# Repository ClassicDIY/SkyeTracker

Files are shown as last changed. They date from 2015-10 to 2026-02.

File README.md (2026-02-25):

# SkyeTracker

<a href="https://www.buymeacoffee.com/r4K2HIB" target="_blank">Buy Me A Coffee</a>




## Dual Axis solar tracker.

This project uses a pair of linear actuators to move a set of solar panels so that they face the sun throughout the day.
Knowing the latitude, longitude and the date/time, the software calculates the azimuth and elevation of the sun. The system is setup and calibrated using an Android app that communicates with the device using the Bluetooth interface. It has support for an anemometer, moving the solar panel array to horizontal position when the wind exceeds 30km/h.

Check the <a href='https://github.com/ClassicDIY/SkyeTracker/wiki'> wiki </a> for more information.

Here are some <a href='https://www.youtube.com/playlist?list=PLblHpNAh7b6LoXEqofkJhKn6jD81Y85qT'> videos </a>.

<p align="center">
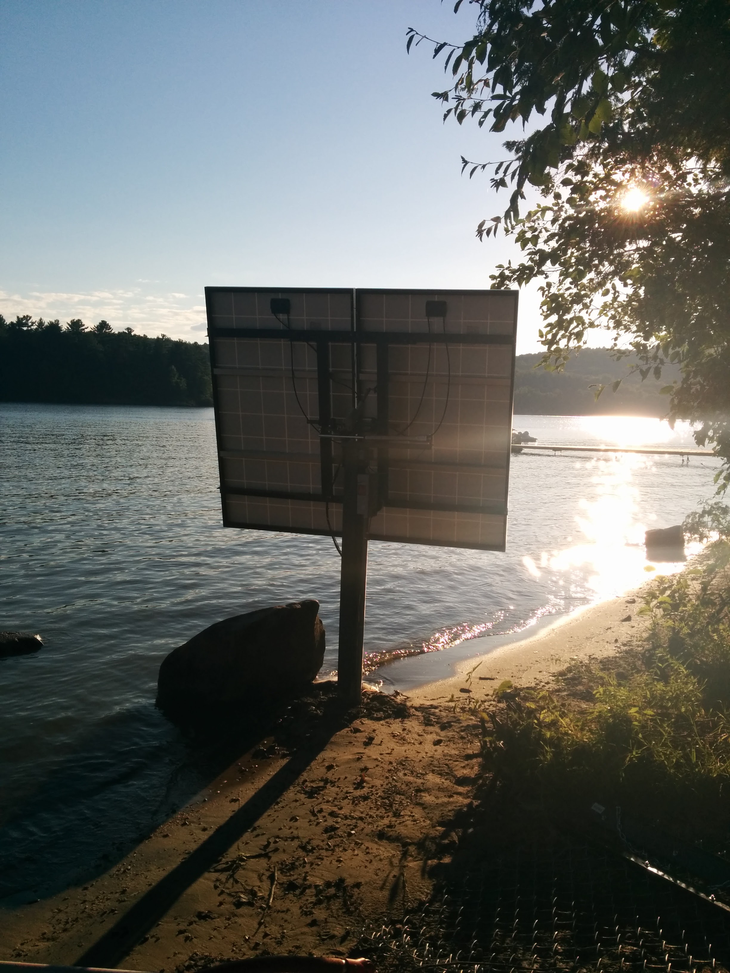
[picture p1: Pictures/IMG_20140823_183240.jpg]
  
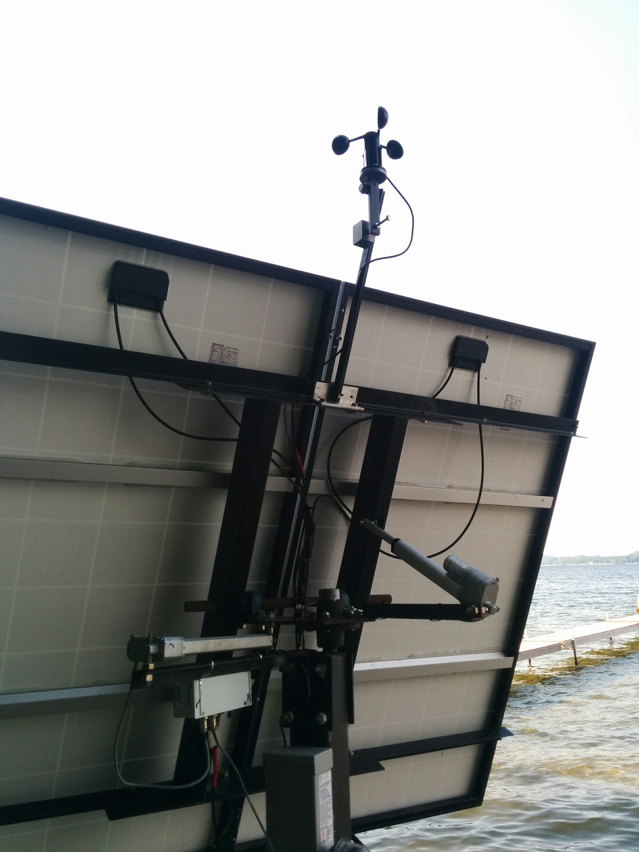
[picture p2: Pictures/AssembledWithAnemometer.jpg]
  
</p>

## SkyeTracker Wiring (Lilygo-T-Relay-S3)

New version 3 for the <a href='https://lilygo.cc/products/t-relay-s3'>Lilygo T-Relay-S3</a>

Note: Classic Bluetooth is no longer supported on the ESP32-S3 (now BLE only), support for the Android app has been removed.
The settings can be accessed via the Wifi Access Point, default AP: SkyeTracker default admin PW: 12345678

<p align="center">
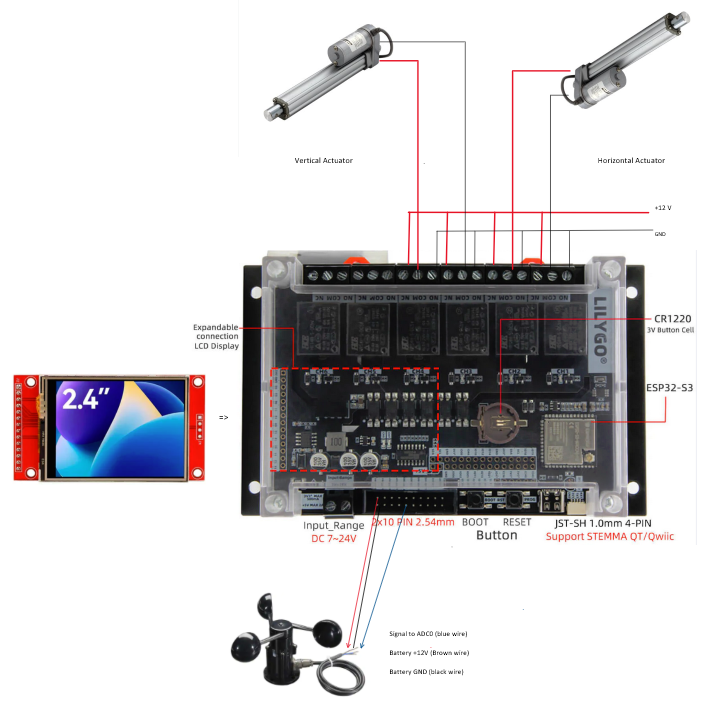
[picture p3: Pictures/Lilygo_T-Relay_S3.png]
  
</p>

<p align="center">
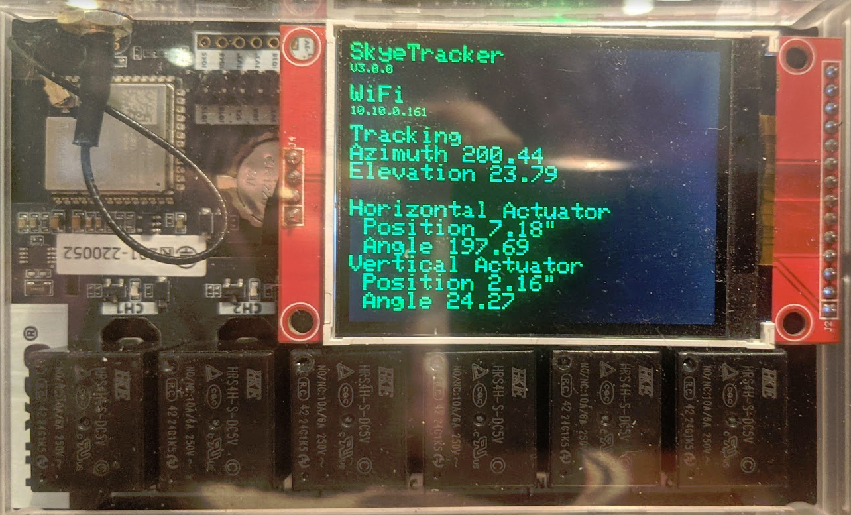
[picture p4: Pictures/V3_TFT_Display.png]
  
</p>

<p align="center">
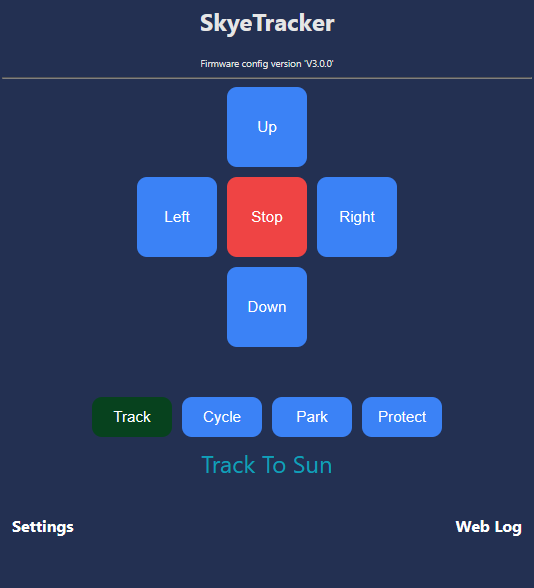
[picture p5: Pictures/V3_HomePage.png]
  
</p>

<p align="center">
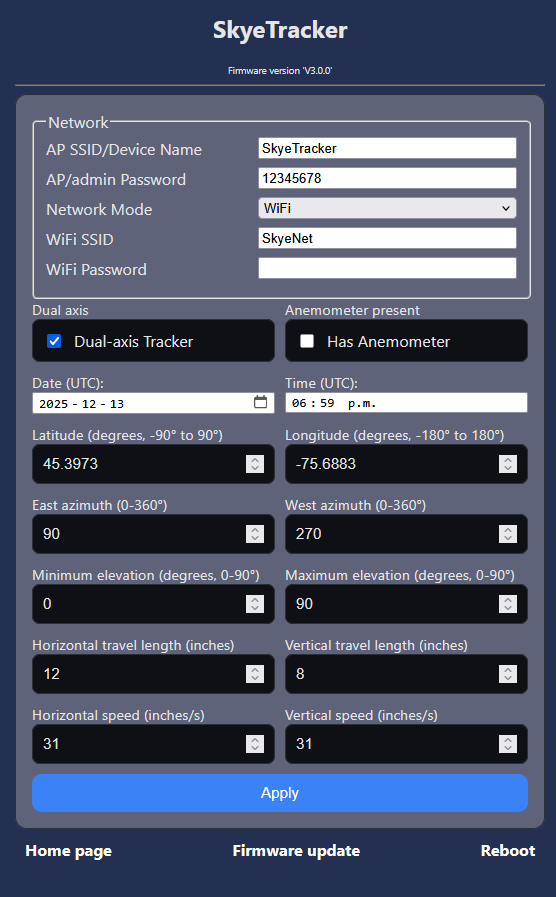
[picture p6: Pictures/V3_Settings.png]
  
</p>

<p align="center">
  
</p>

## SkyeTracker Wiring (ESP32 version 2)

Check the [wiki](https://github.com/ClassicDIY/SkyeTracker/wiki/4---ESP32-wiring-diagram) for updated information on the ESP32 implementation.

<p align="center">
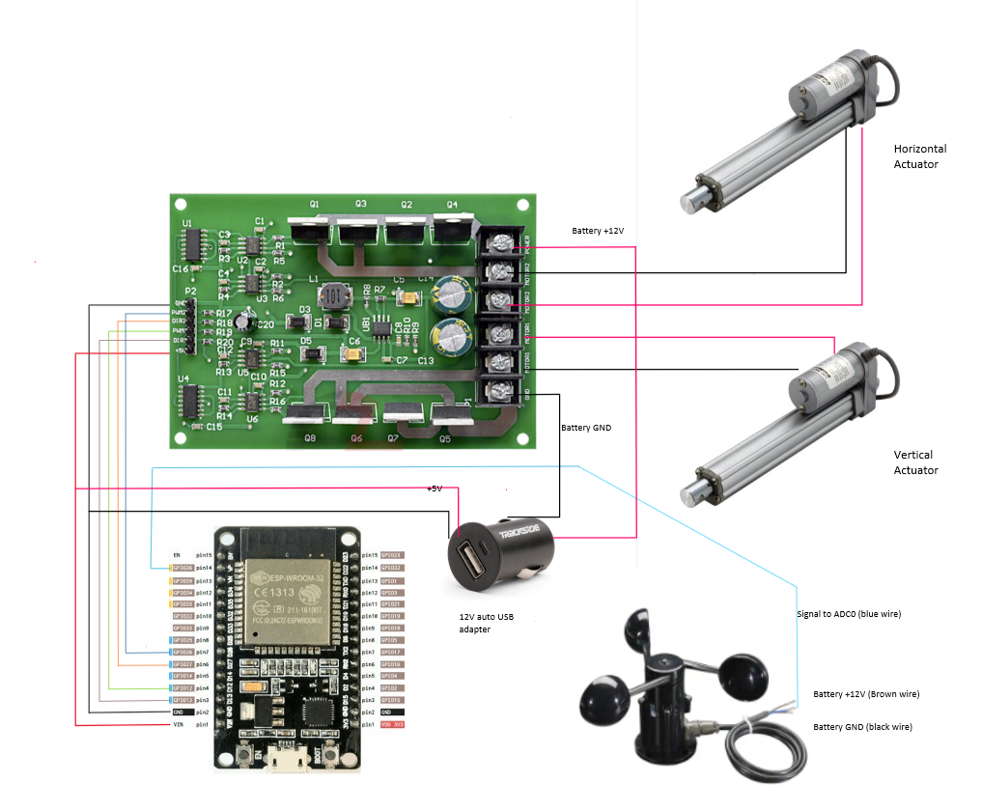
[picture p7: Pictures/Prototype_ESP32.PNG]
  
</p>

## Development tools:

<ul>
  <li>Visual Studio Code with PlatformIO IDE extension.</li>
  <li>Diptrace for schematic & PCB (NANO version).</li>
  <li>Sketchup for mechanical drawings.</li>
</ul>

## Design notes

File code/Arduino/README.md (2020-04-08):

# Arduino version of SkyeTracker 

<p align="center">
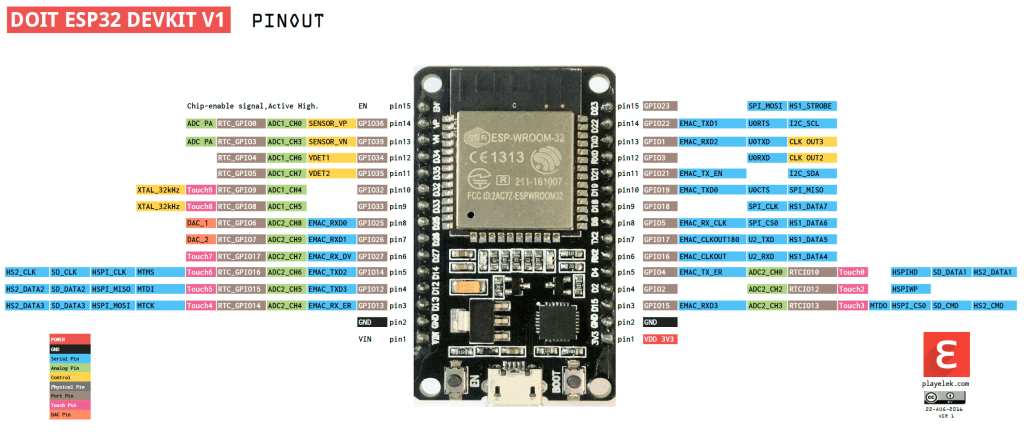
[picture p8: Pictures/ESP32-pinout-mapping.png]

</p>

Please refer to the [SkyeTracker wiki](https://github.com/ClassicDIY/SkyeTracker/wiki) for more information.

# Programming setup for the Arduino version of SkyeTracker

Once you downloaded and extracted the ZIP file for this project,
the code for the Arduino implementation is available in the `SkyeTracker-master\code\Arduino\SkyeTracker` directory.

This project uses Visual Studio CODE with the PlatformIO extension.
Here is a video tutorial for the VSCode & PlatformIO setup;
[PlatformIO for ESP32 Tutorial](https://www.youtube.com/watch?v=0poh_2rBq7E)

Once setup with the PlatformIO extension, use File->Open Folder to open the project selecting the `SkyeTracker-master\code\Arduino\SkyeTracker` folder.

The Arduino type can be set in the platform.ini.

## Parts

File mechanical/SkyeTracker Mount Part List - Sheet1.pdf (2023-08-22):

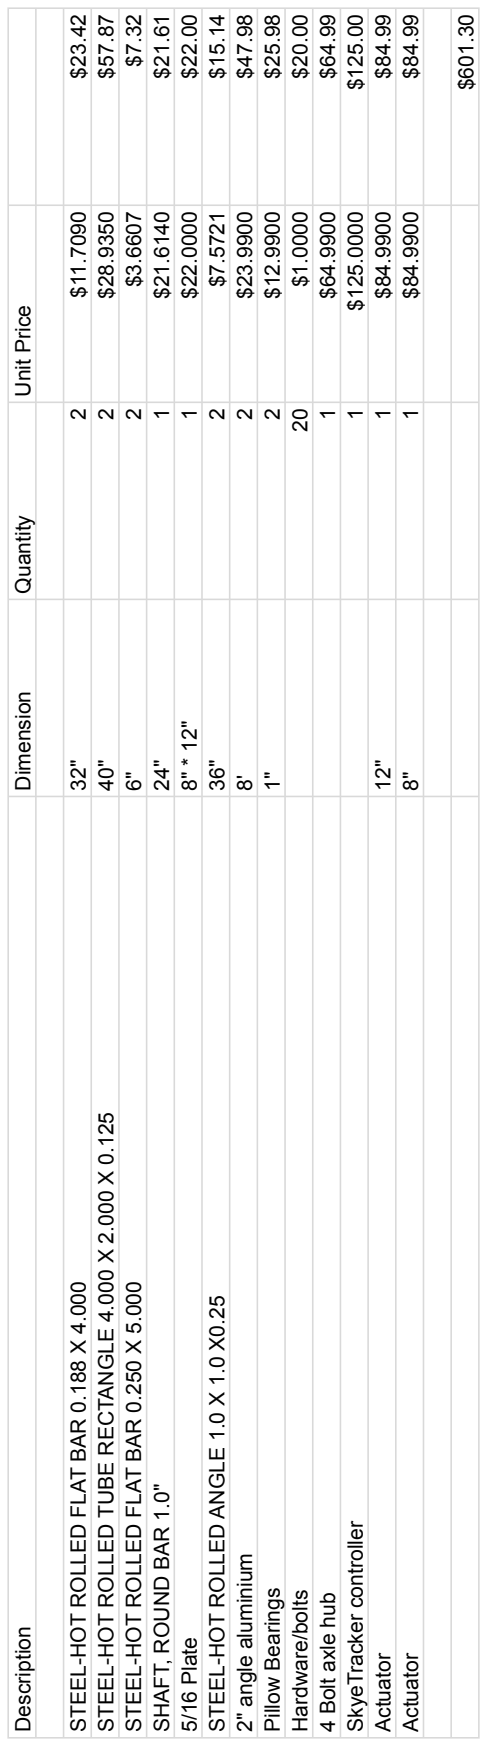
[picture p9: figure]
5/16 Plate 8" * 12" 1 $22.0000 $22.00; 2" angle aluminium 8' 2 $23.9900 $47.98; Pillow Bearings 1" 2 $12.9900 $25.98; Hardware/bolts 20 $1.0000 $20.00; 4 Bolt axle hub 1 $64.9900 $64.99; Actuator 12" 1 $84.9900 $84.99; Actuator 8" 1 $84.9900 $84.99

Description Dimension Quantity Unit Price

STEEL-HOT ROLLED FLAT BAR 0.188 X 4.000 32" 2 $11.7090 $23.42

STEEL-HOT ROLLED TUBE RECTANGLE 4.000 X 2.000 X 0.125 40" 2 $28.9350 $57.87

STEEL-HOT ROLLED FLAT BAR 0.250 X 5.000 6" 2 $3.6607 $7.32
SHAFT, ROUND BAR 1.0" 24" 1 $21.6140 $21.61

STEEL-HOT ROLLED ANGLE 1.0 X 1.0 X0.25 36" 2 $7.5721 $15.14 SkyeTracker controller 1 $125.0000 $125.00

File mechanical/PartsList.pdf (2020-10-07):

Description | Dimension | Length | Quantity | Price per foot | Unit Price | Price
Foot plate | 8" X .250 Flat bar | 8" | 1 | $17.80 | $12.00 | $12.00 metalsupermarkets.com
Gussets for foot plate | | | 8 | | $2.00 | $16.00
Post | 5" X 5" X .188" Square Tube | 60" | 1 | $24.00 | $120.00 | $120.00
Hub mounting plate | 5" X .188" Flat bar | 5 | 2 | $11.00 | $4.50 | $9.00
Bolts & Nuts for Hub plate | 3/8" X 6" | | 4 | | $2.00 | $8.00
Rotator Plate | 12" X 3/8" Flat bar | 12" | 1 | $30.00 | $30.00 | $30.00
Horizontal actuator arm | 1" X 1" angle | 23 3/8" | 1 | $7.00 | $14.00 | $14.00
Horizontal actuator arm mounting plate | 1" flat bar | 5" | 1 | $6.00 | $3.00 | $3.00
Horizontal actuator arm gusset | | | 1 | | $2.00 | $2.00
Vertical actuator arm | 1" X 1" angle | 15" | 1 | $7.00 | $8.75 | $8.75
H frame shaft | 1" | 23" | 1 | $10.00 | $19.20 | $19.20
H frame square tube | 4" X 2" X 0.125" square tube | 40" | 2 | $18.00 | $60.00 | $120.00
H frame end plates | 4" X 0.188" flat bar | 32" | 2 | $8.91 | $27.77 | $55.54
H frame sleeve | 3" X 1" I.D. | | 2 | | $11.80 | $23.60 Steel sleeve
Pillow Bearings | 1" | | 2 | | $12.18 | $24.36 Pillow-Block-Cast-Housing-Mounted
Bolts & Nuts for pillow bearings | 3/8" | 1.5" | 4 | | $1.50 | $6.00
4 Bolt axle hub | | | 1 | | $79.99 | $79.99 stub axle
SkyeTracker controller with box | | | 1 | | $100.00 | $100.00
Actuator | 12" | | 1 | | $84.99 | $84.99 12in linear actuator
Actuator | 8" | | 1 | | $84.99 | $84.99 8in linear actuator

$821.42

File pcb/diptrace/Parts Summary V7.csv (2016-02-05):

SkyeTracker V7
Column1 | Column2 | Column3
Part | Quantity | Stock | Unit Price | Sum | Link
CR1220 3.3v Lithium Coin Cells Button Battery | 1 | 21 | 0.194800 | $0.194800
CR1220 3.3v Lithium Coin Cells Button Battery holder | 1 | 1 | 0.650000 | $0.650000
50V 220UF SMD Aluminum Electrolytic Capacitors Size 10*10.2MM | 1 | 7 | 0.554500 | $0.554500
35v 220UF SMD Aluminum Electrolytic Capacitors Size 8x10mm | 2 | 54 | 0.708500 | $1.417000
0.1uf Ceramic capacitors SMD 0603 | 2 | 20 | 0.007327 | $0.014654
DO-214AC M7 SMA IN4007 SMD 1A | 8 | 63 | 0.049900 | $0.399200
SCHOTTKY SS54 5A 40V DO-214AC | 2 | 16 | 0.170000 | $0.340000
SMD 0805 Blue LED | 1 | 100 | 0.013720 | $0.013720
1206 SMD Resettable Fuse DC:32V 3A | 1 | 2 | 0.268000 | $0.268000
1206 SMD Resettable Fuse DC:32V 2A | 2 | 47 | 0.268000 | $0.536000
2Pin Plug-in Screw Terminal Block Connector 3.81mm Pitch Right Angle Orange | 1 | 20 | 0.543500 | $0.543500
2Pin Plug-in Screw Terminal Block Connector 3.81mm Pitch Right Angle Green | 2 | 20 | 0.720000 | $1.440000
INDUCTOR 12X12mm | 1 | 7 | 0.471000 | $0.471000
2.2k Resistor SMD 1206 | 2 | 100 | 0.005552 | $0.011104
634 Resistor SMD 1206 | 1 | 100 | 0.005552 | $0.005552
40pin Strip Tin PCB Female IC Breakable Single Row | 1 | 3 | 0.667000 | $0.667000
Arduino Nano V3.0 ATmega328 | 1 | 4 | 3.132000 | $3.132000
DS1307Z SMD SOP-8 | 1 | 9 | 0.130600 | $0.130600
HC_06 Bluetooth RF Transceiver Module | 1 | 4 | 4.134000 | $4.134000
L298N ZIP-15 ST DUAL FULL BRIDGE MOTOR DRIVER | 1 | 10 | 1.434000 | $1.434000
Screw for heat sink, 2.7 * 6mm | 1 | 10 | 0.059000 | $0.059000
Black Aluminum Heat Sink Heatsink for TO220 L298N | 1 | 7 | 0.443000 | $0.443000
LM2596S-12 TO-263 LM2596 12V Voltage Regulator | 1 | 4 | 0.693000 | $0.693000
SMD-2Pin 32.768K 32.768KHz Crystal 3.2mm×1.5mm | 1 | 40 | 1.384000 | $1.384000
PCB | 1 | 2 | 13.500000 | $13.500000
158x90x65mm Clear Waterproof Plastic Electronic Project Box Enclosure Cover CASE | 1 | 0 | 6.990000 | $6.990000 | http://www.ebay.ca/itm/158x90x65mm-Clear-Waterproof-Plastic-Electronic-Project-Box-Enclosure-Cover-CASE-/262063317709
Nylon Plastic stick on PCB Locking Snap-In Spacer Standoff 3mm Hole | 4 | 0 | 0.140500 | $0.562000 | http://www.ebay.ca/itm/221939473950?var=520828301848
Strain Relief Bushing for 5mm Round Cables | 3 | 0 | 0.080800 | $0.242400 | http://www.ebay.ca/itm/50pieces-Nylon-Wires-Protectors-Strain-Relief-Bushing-for-5mm-Round-Cables-/351136555494
 |  |  |  | $40.230030

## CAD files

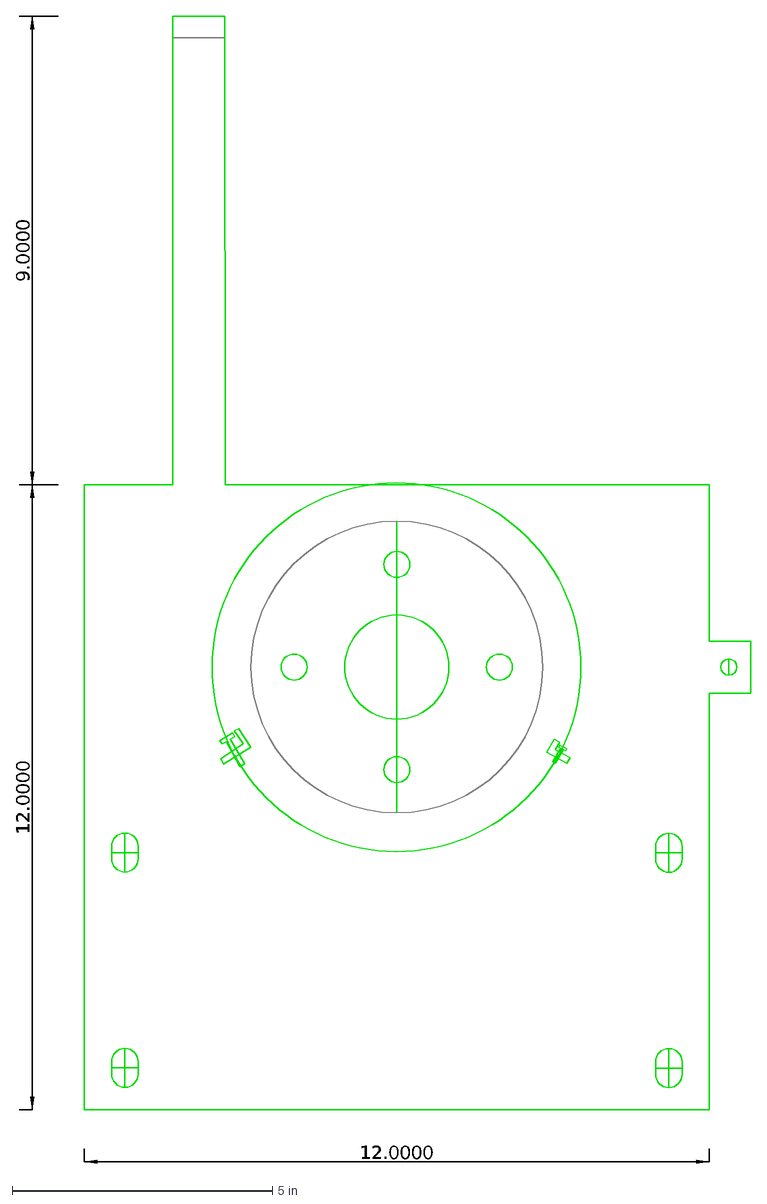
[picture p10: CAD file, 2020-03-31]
mechanical/LibreCAD/Bottom.dxf
9.0000
12.0000

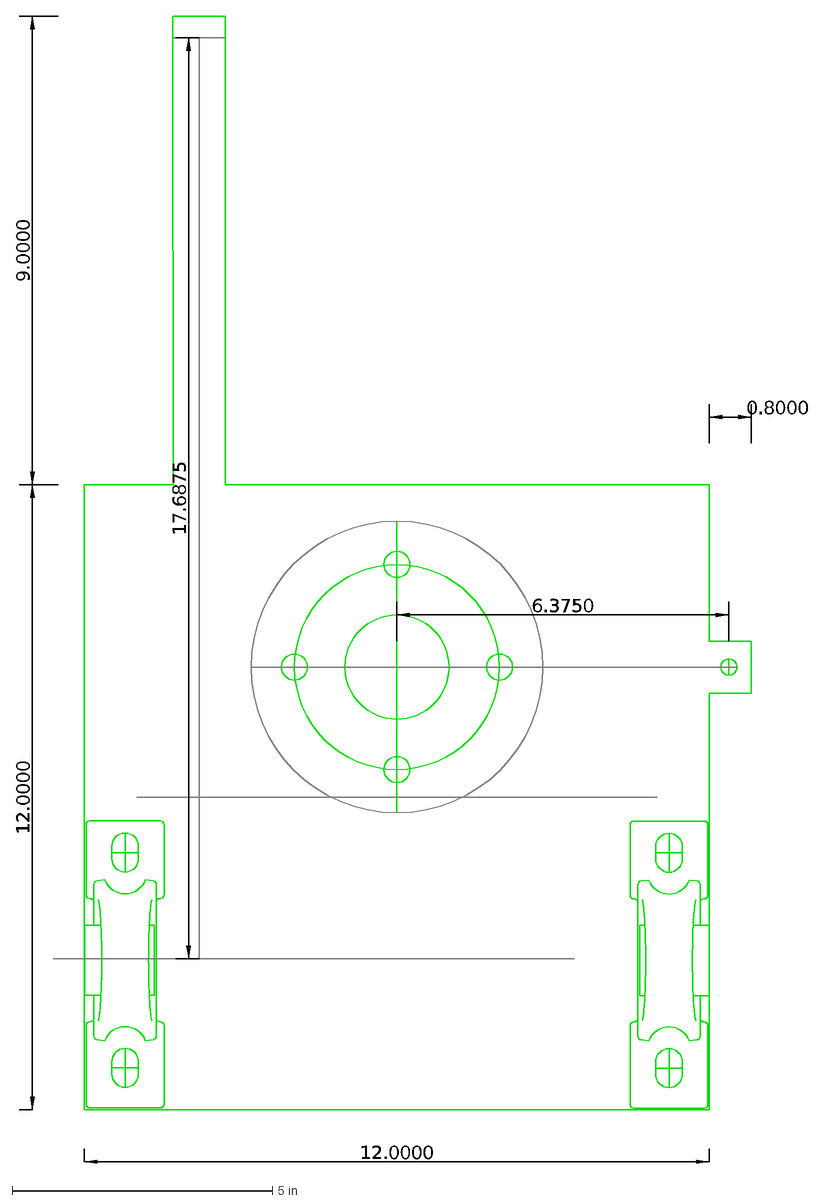
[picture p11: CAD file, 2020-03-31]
mechanical/LibreCAD/hub.dxf
6.3750
17.6875
9.0000
12.0000
0.8000

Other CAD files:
mechanical/TrackerFrame/Drawings/StubAxle.dwg
mechanical/Archive/Sketchup/Components/8L16.skp
mechanical/Archive/Sketchup/Components/FRAME2.skp
mechanical/Archive/Sketchup/Components/Linear Actuator 12 inch.skp
mechanical/Archive/Sketchup/Components/Linear Actuator 6 Inch.skp
mechanical/Archive/Sketchup/Components/Solar Panel 60 cell Kyocera.skp
mechanical/Archive/Sketchup/Components/Solar Panel 72 cell.skp
mechanical/Archive/Sketchup/Components/Vent.skp
mechanical/Archive/Sketchup/Models/Battery Box.skp
mechanical/Archive/Sketchup/Models/Dual Axis Tracker Assembly.skp
mechanical/Sketchup/Components/8L16.skp
mechanical/Sketchup/Components/FRAME2.skp
mechanical/Sketchup/Components/Linear Actuator 12 inch.skp
mechanical/Sketchup/Components/Linear Actuator 6 Inch.skp
mechanical/Sketchup/Components/Solar Panel 60 cell Kyocera.skp
mechanical/Sketchup/Components/Solar Panel 72 cell.skp
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

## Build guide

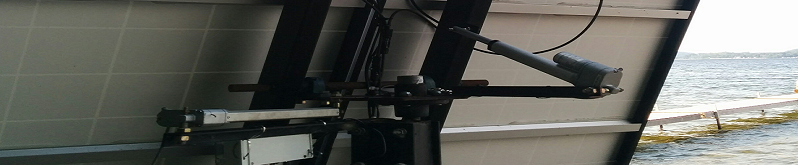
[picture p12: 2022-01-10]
Pictures/AssembledWithAnemometer_small.png

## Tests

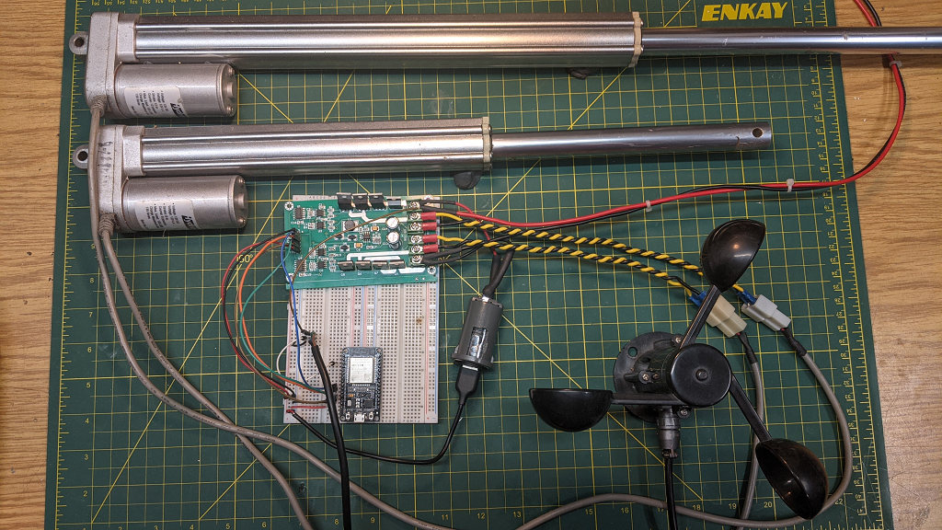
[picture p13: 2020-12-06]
Pictures/TestCircuit.png

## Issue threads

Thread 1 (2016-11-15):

adding a "skew" setting?

Paul-Bostwck, 2016-11-15:
Hey...

I'm hoping to find a tracking program for my tip and roll array collector. The extra tricky bit is that my collector is made of a group of tubes that contain optics that need two axis tracking (so far so good) But the tubes are anchored at the foot and turn on the central axis for east west and so tip up and down at the top for north south. The hard bit is installation of the array can be along non east west lines (in the graphic that is the foot line) so there needs to be compensating math for the difference... any ideas about how to implement those "corrections" in the code?
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

Paul-Bostwck, 2016-11-15:
Those tubes are the collector surfaces... the sun is at the top of the image shining down on the tubes.

graham22, 2016-11-15:
I suppose you could modify the run function in the linearActuator code, the
current implementation assumes a linear movement/positioning, ie one inch
of travel equals a given angle of movement, you could add a function to
calculate a non-linear position to angle.
I'm not sure if this would be accurate enough for what your doing, you
might need actuators with position feedback...

On Tue, Nov 15, 2016 at 12:03 PM, Paul-Bostwck <notifications@github.com>
wrote:

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

--
Graham A. Ross
(613) 769-1331

Paul-Bostwck, 2016-11-17:
Hey Graham22
thanks for responding!
I think you described it well (I have a hacking session with a clever friend this weekend and this way of describing the problem will likely help)
I suspect you are right: the position feedback is very likely to be needed. I do have the advantage of a large diameter az wheel (.1m) and the length of the tubes (1.8m) as the radius of the elevation "gear" , so many stepper turns will add up to very small movements of the system but even still, "where are we" will need some kind of verification system.
The non-linear aspect of the function is going to squeeze my brain hard! I guess both axis will have their own adaptation and together they should arrive at the aim...
OK up too late. Thanks for the feedback. More as I know it!

Another image of my collector design, for your entertainment:
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

Paul-Bostwck, 2016-11-17:
That is a section view of a section of one of the tubes.

graham22, 2020-04-16:
The code assumes linear actuators

Closed 2020-04-16.

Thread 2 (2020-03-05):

anemometer in fritzing sketch

thijstriemstra, 2020-03-05:
cool project! I'm looking at https://github.com/graham22/SkyeTracker/blob/master/Pictures/Prototype%20parts%20list.PNG and the fritzing sketch and i don't see the wind sensor anywhere. is there an updated version of the fritzing sketch? :) Also, what resistors are you using there @graham22?

graham22, 2020-03-06:
I used the [anemometer ](https://www.adafruit.com/product/1733)from Aidafruit and measured the output (0.4V to 2.0V)
You can use [diptrace ](https://diptrace.com/download/download-diptrace/)to view the full schematic (NanoTracker L298 L7805 NoPOT V7.dch)

thijstriemstra, 2020-03-06:
thanks for the feedback. I ordered one of these, hopefully it'll work out https://www.ebay.com/itm/12V-24V-Wind-Speed-Sensor-Voltage-Signal-Output-Anemometer-Fit-for-Outdoor-Use/201249466834

Also ordered the other parts from your list. Will first try to setup everything using one of these controllers: https://www.ebay.com/itm/Dual-Axis-Solar-Tracking-Tracker-Controller-for-PV-Solar-Panel-System-Sun-Track/191406191627

And then move the system to Arduino. If I end up using your code I will try to contribute a web interface. I guess this will need an ESP32 module running a webserver? I'm new to Arduino.

graham22, 2020-03-06:
I"m also working on a ESP32 implementation of the tracker, all you would need is an ESP32 dev board with a motor controller like [this one](https://www.banggood.com/DC-3-36V-15A-Peak-30A-PWM-DC-Dual-Channel-Motor-Driver-Board-High-Power-H-Bridge-Control-Module-p-1255708.html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).
The code is under code/ESP32/SkyeTracker in github, i used VSCode with the PlatformIO plug in

thijstriemstra, 2020-03-07:
I added a parts list on the wiki page: https://github.com/graham22/SkyeTracker/wiki

can you check if this is correct? and I couldn't find any bluetooth references in the Arduino sketch (yet), is this correct and is it only used in esp32 version, or did i miss the references in the code?

graham22, 2020-03-07:
thanks, looks correct for the arduino version, the esp version doesn't need
the HC-06 or the RTC since it can get the dateline from the internet and
has built in BT

since the arduino version is using a HC-06 it communicates with the arduino
over a serial port

On Sat, Mar 7, 2020 at 2:57 PM Thijs Triemstra <notifications@github.com>
wrote:

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

--
Graham A. Ross
(613) 769-1331

thijstriemstra, 2020-03-08:
> the esp version doesn't need the HC-06 or the RTC

I still see references to the ds1307 in the esp32 code though, e.g. https://github.com/graham22/SkyeTracker/blob/master/code/ESP32/SkyeTracker/src/Configuration.cpp#L4

And also a hc-06 reference, but I can see how it's a simple string and not tied to implementation: https://github.com/graham22/SkyeTracker/blob/master/code/ESP32/SkyeTracker/src/main.cpp#L143

graham22, 2020-03-08:
I should rename the define to STORAGE_SIZE

On Sat, Mar 7, 2020 at 7:41 PM Thijs Triemstra <notifications@github.com>
wrote:

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

--
Graham A. Ross
(613) 769-1331

thijstriemstra, 2020-03-08:
> I should rename the define to STORAGE_SIZE

I will take a look and open a pull request.

graham22, 2020-03-08:
We should also make a separate wiki page for the arduino and the ESP32
since the ESP is 3.3 volts, it should not be used with a regular L298

On Sun, Mar 8, 2020 at 11:51 AM Thijs Triemstra <notifications@github.com>
wrote:

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

--
Graham A. Ross
(613) 769-1331

thijstriemstra, 2020-03-08:
sounds good. I've ordered a new ESP32, but have others if this one might cause issues somehow: https://www.ebay.com/itm/ESP-32-ESP32S-Development-Board-2-4GHz-WiFi-Bluetooth-Antenna-CP2102-Module/152479854433

What specific ESP32 device are you using?

thijstriemstra, 2020-03-08:
I see the anemometer vars are hardcoded in `Anemometer.h`:

```c++
//Anemometer Technical Variables
//The following variables correspond to the anemometer sold by Adafruit, but could be modified to fit other anemometers.
#define voltageMin .4 // Mininum output voltage from anemometer in mV.
#define windSpeedMin  0 // Wind speed in meters/sec corresponding to minimum voltage
#define voltageMax 2.0 // Maximum output voltage from anemometer in mV.
#define windSpeedMax 32 // Wind speed in meters/sec corresponding to maximum voltage
```

I'll be using different values so can this be moved to a `build_flags` in `plaformio.ini`?

graham22, 2020-03-08:
ESP-WROOM-32

On Sun, Mar 8, 2020 at 12:27 PM Thijs Triemstra <notifications@github.com>
wrote:

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

--
Graham A. Ross
(613) 769-1331

graham22, 2020-03-08:
ok

On Sun, Mar 8, 2020 at 1:25 PM Thijs Triemstra <notifications@github.com>
wrote:

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

--
Graham A. Ross
(613) 769-1331

thijstriemstra, 2020-03-08:
Let me figure out how to do that. Can you also take a look at pull request #4?

thijstriemstra, 2020-03-08:
> I should rename the define to STORAGE_SIZE

Opened pull request #6 for this.

graham22, 2020-03-08:
merged all the pull requests

BTW, the ESP version has support for MQTT that is not implemented in the
Arduino version
you can use a tool like mqttfx <https://mqttfx.jensd.de/index.php/download> to
control the tracker and receive 'discovery' information
I was planning on integrating it into home assistant
<https://www.home-assistant.io/docs/>

On Sun, Mar 8, 2020 at 1:28 PM Thijs Triemstra <notifications@github.com>
wrote:

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

--
Graham A. Ross
(613) 769-1331

thijstriemstra, 2020-03-08:
> BTW, the ESP version has support for MQTT that is not implemented in the Arduino version

Very cool, can't wait to try it out, the actuators arrive thursday.

thijstriemstra, 2020-03-22:
> We should also make a separate wiki page for the arduino and the ESP32 since the ESP is 3.3 volts, it should not be used with a regular L298

Created separate wiki pages:

- https://github.com/graham22/SkyeTracker/wiki/Arduino
- https://github.com/graham22/SkyeTracker/wiki/ESP32

Closed 2020-03-08.

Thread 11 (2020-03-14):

Using bigger motor controller

thijstriemstra, 2020-03-14:
The actuators I'm using need 3A each (at peak) and we decided to use 2 BTS7960 motor controllers.

There is a https://github.com/eicke123/BTS7960Library Arduino library for BTS7960 that seems to do the same. Any ideas on how to extend the `LinearActuatorNoPot` class? Could you add an interface that can be extended (I'm new to C++) with different types of Actuator implementations?

thijstriemstra, 2020-03-14:
If you're interested in testing I can always order and send you such a BTS7960.

graham22, 2020-03-14:
I don't think you need that library
it's used to control the motor speed using PWM (Pulse Width Modulation),
the motor on the actuators are either off (0V) or full speed (12V)

I used this board
<https://www.aliexpress.com/item/32821835744.html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,searchweb201602_,searchweb201603_>
with
the ESP32 pins as defined in the platform.ini file, the code sets PWMa
high/low & PWMb low/high to set the direction then enable to run the
actuator for the amount of time required.

[image: image.png]

line 147 LinearActuatorNoPot.cpp
[image: image.png]

On Sat, Mar 14, 2020 at 6:47 PM Thijs Triemstra <notifications@github.com>
wrote:

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

--
Graham A. Ross
(613) 769-1331

thijstriemstra, 2020-03-15:
I see. This setup looks similar to what you're describing: https://www.youtube.com/watch?v=QvXa6GKLu6E I'll give it a try asap.

thijstriemstra, 2020-03-16:
Managed to get the actuator working using 3 signals and it should work same as SkyeTracker setup.

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

Note that `PWM` covers 2 pins on the BTS7960: `L_EN` and `R_EN` receive the same signal from the ESP32.

Closed 2020-03-21.

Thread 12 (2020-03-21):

WIFI_STATUS_PIN and WIFI_AP_PIN

thijstriemstra, 2020-03-21:
What are the pins `WIFI_STATUS_PIN` and `WIFI_AP_PIN` being used for?

See https://github.com/graham22/SkyeTracker/blob/master/code/ESP32/SkyeTracker/platformio.ini#L51

graham22, 2020-03-21:
Those can be removed,
the IotWebConf library has options to set the status and AP pins to indicate and trigger AP mode.
the code currently uses setApTimeoutMs(30000) instead.

thijstriemstra, 2020-03-21:
> Those can be removed,

Ok, will do.

thijstriemstra, 2020-03-22:
see #13

Closed 2020-03-22.

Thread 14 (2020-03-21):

anemometer sensorVoltage calculation

thijstriemstra, 2020-03-21:
What are these values in code/ESP32/SkyeTracker/src/Anemometer.cpp

```
double sensorVoltage = -0.000000000000016 * pow(reading, 4) + 0.000000000118171 * pow(reading, 3) - 0.000000301211691 * pow(reading, 2) + 0.001109019271794 * reading + 0.034143524634089;
```

can you add some code comments for this? do these constants change when using a different anemometer?

graham22, 2020-03-21:
comes from this
i would not change them

https://github.com/G6EJD/ESP32-ADC-Accuracy-Improvement-function/blob/master/ESP32_ADC_Read_Voltage_Accurate.ino

On Sat, Mar 21, 2020 at 10:17 AM Thijs Triemstra <notifications@github.com>
wrote:

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

--
Graham A. Ross
(613) 769-1331

thijstriemstra, 2020-03-21:
Thanks, I will document that.

Closed 2020-03-24.

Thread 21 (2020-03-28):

Checking for movements

sgamix, 2020-03-28:
Hi, I downloaded your project and I must say it is fantastic. I don't have all the materials you used, for example I don't have linear motors but I simulated the outputs by connecting LEDs to see how it behaves.
I noticed that after some time the program sends the movements.
The questions are:
How long does it take between chasing?
Which sensors are needed to know the status of the trak?

The last question is for a safety issue, putting the case of not using linear motors but simply normal 24V dc gearmotors.
How do I know how the traker is moving and where it got there?

Another question, is it possible to remove the configuration via the Android App and simply use the Arduino Sketch ??
This question is why I don't know Android Studio and I don't need to enter the coordinates by phone, I already know the coordinates.
The problem of manual movement will always remain if I do not have the Android App, but I will try to move it through external selectors.
My intent is to test your project on an existing photovoltaic system where 158 Traker columns with a 30-panel sail are currently installed.
Currently the trakers have their controller that makes the motors move and through two sensors (10K potentiometer for azimuth and 2-axis sensor for elevation) it controls the movement in the right direction. If I can, I attach the photo of the system.

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

Thanks

Fabio

graham22, 2020-03-28:
Hi Fabio,
I recently setup a slack channel for some of my github projects if you would like to join to see some of the discussions relating to SkyeTracker
[https://join.slack.com/t/classicdiy/shared_invite/zt-czhgndgj-o5RuQ6K6d7yXg309ShXKbQ](url)

I'm working on a new version that uses the ESP32 chip that has MQTT for setup and status.
The code uses astronomical solar tracking so no sensors are required.
The actuators speed and limits are calibrated in the app so position feedback is not required.

Graham

Closed 2020-03-29.

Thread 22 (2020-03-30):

Move Anemometer to separate library

thijstriemstra, 2020-03-30:
I'd like to use the Anemometer class in other non-SkyeTracker projects as well. Can it be moved to a separate repository/project so it can be used by other Arduino projects? Feel free to add me as a team member, I can help out with this.

thijstriemstra, 2020-03-30:
thanks @graham22, I'm now a member. Maybe you can import the classes into a new repository (with vscode/platformio type structure), something like https://github.com/SkyeTracker/anemometer?

thijstriemstra, 2020-03-30:
And what do you suggest to call the main repository, something like SkyeTracker-core? I think the Android code should also have it's own repository. Would be cool if the new repositories get their code imported in a such a way that the git log history is retained.

graham22, 2020-03-30:
I'm not sure I want to split everything up,  I have Jonas working on the CAD drawings and I have the hardware PCBs  where would these go?

thijstriemstra, 2020-03-30:
Alright, I see your point. I would move all documentation related things like that in a `doc` dir in root of repository. Perhaps we can use sphinx documentation tool to generate some nice documentation and move away from the wiki.

ps. I can also make the anemometer repository but then the code will not contributed to you in the git history, that's why I'm asking you to add the intial classes.

graham22, 2020-04-16:
Make a copy of the library for your use

Closed 2020-04-16.

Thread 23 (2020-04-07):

Movement and communication problems

sgamix, 2020-04-07:
Good evening,
I tried the project on Arduino UNO with HC-06 module, DS1307, L298N and 2 5 volt motors.
I have modified the SoftwareSerial with pins 8, 9 in the SkyeTracker.ino file and through a software installed on an Android phone I receive the data from the module.
Starting Arduino I receive the following messages from the HC-06:
RAM in Run: 358
RAM At start of setup: 801
2020/4/7 16:50:11
Loading Configuration
Initializing tracker
RAM Completing setup:
801
TrackToSun (I get this often if I keep it on)

By switching to the SkyeTraker app, however, I do not receive anything on the INFO page and even going to change the LIMITS, LOCATION, DATE / TIME parameters, nothing happens on the Arduino.
By manually trying from MOVE nothing happens.

But when Arduino starts, the motors turn first in one direction and then the other, after starting on the serial I read the change data but the motors no longer move.

That it is a problem of L298N is to be excluded because I tried a program to make them move and they do it safely.
I don't understand why the startup works and then nothing moves.

The biggest problem is understanding why I can't communicate with Arduino from the App, I installed it on Android 10, Android 8 and even Android 4.4

No data in all 3 devices

Regards

Fabio

graham22, 2020-04-07:
Hi Fabio
it looks like you have the logs going to the HC-06,
the code uses 2 serial ports, the sofwareSerial is for logging purposes to the console and the standard serial should go to the HC-06 for the android app and should be sending JSON data.

Graham.

sgamix, 2020-04-08:
Hello,
apart from the data on the Android App which would be the minimum.
I connected the LEDs to the Arduino outputs, 2 red for movement enablement and 4 green for movement.
The LEDs light up Red - Green only when Arduino is started, after the start of the serial the message of the current chase appears but the LEDs do not light up.
Where is the problem ??
The code is little commented and it is not easy to find the lines concerned.
As for JSON, the version of your program is 5 and going to 6 I have to recompile a lot of stuff and since it doesn't work as normal I don't see the reason to start recompiling if it doesn't work.
That the program has two serial numbers, I realized it and HC-06 uses that _sw software that I have to set it to 9600 because the module has that speed.

Having said that, the trak does not chase anything since startup is complete, so the problem is great on the main operating logic, HC-06 or any Wifi go into the background in my opinion.

Thanks

sgamix, 2020-04-08:
Hello,
the problem concerns programming, if HC-06 is connected as per your diagram (0 RX - 1 TX) Arduino cannot be programmed. To get around the problem I have to remove the TX and RX.
So if HC-06 worked on _sw Serial it would have been better as it does not use the pins it normally uses for programming.
Having said that, I noticed that the LEDs light up in a strange way, I would like to understand if in the Tracker.cpp file the following code is the pin assignment for the motors

_azimuth = new LinearActuatorNoPot ("Horizontal", PIN7, PIN2, PIN3);
controller-> add (_azimuth);
_elevation = new LinearActuatorNoPot ("Vertical", PIN6, PIN4, PIN5);

Thanks

graham22, 2020-04-08:
This code was written over 5 years ago, it's going to be a lot of work to
upgrade it to use the current dependencies.
I would suggest you use the ESP32 version ($5 on ALiexpress
<https://www.aliexpress.com/item/32800930387.html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>)
which is more recent.

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

--
Graham A. Ross
(613) 769-1331

graham22, 2020-04-08:
Ok, I ported the arduino code to VSCode, upgraded ArduinoJSON
Tested it on my nano board and everything works with the android app.
You can try the UNO version by changing it in platform.ini

sgamix, 2020-04-09:
Thanks for the JSON update, I will always test everything on Arduino UNO because I have the one for the moment.

Closed 2020-04-16.

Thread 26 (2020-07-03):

Nach Sonnen Untergang wieder in anfangsstellung gehen

jens-software, 2020-07-03:
Gibt es auch Funktion das nach Sonnenuntergang die Anlage wieder zum Anfang fährt.
German text

thijstriemstra, 2020-07-03:
you can at least use google translate, I have no idea what this means.

graham22, 2020-07-05:
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

WaitForMorning function will retract both actuators

jens-software, 2020-07-14:
Hello
Sometimes a question is the esp8266 necessary or only the arduino is enough
I'm still fairly new to the field and would like to implement the project here with me
Or is there a manual what exactly is needed
Greetings from Germany East Frisia

graham22, 2020-07-14:
You can use either the Arduino Nano or the ESP32 (not esp8266)
I did the Arduino Nano version a few years ago, it's been running at my
cottage since then.
More recently, I ported the code to the ESP32.

The esp32 version is simpler to build since you only need to add the
HBridge to the ESP32 as per the Wiki
<https://github.com/ClassicDIY/SkyeTracker/wiki/3---ESP32>

There is a collaborator from Sweden who has created the mechanical drawings
using Autocad, he has not shared the drawings on github yet but I can put
you in touch with him to see if he would be willing to share the drawings.
[image: image.png]

cheers
Graham.

On Tue, Jul 14, 2020 at 8:01 AM jens-software <notifications@github.com>
wrote:

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

--
Graham A. Ross
(613) 769-1331

jens-software, 2020-07-16:
Ist der Anschluss vom arduino gleich wie der esp32

graham22, 2020-07-16:
Both use the same Android app.
the connections for the arduino are described in the wiki [page2](https://github.com/ClassicDIY/SkyeTracker/wiki/2---Arduino)
the connections for the esp32 are described in the wiki [page3](https://github.com/ClassicDIY/SkyeTracker/wiki/3---ESP32)

jens-software, 2020-07-18:
Hi hab jetzt den esp32 mit wlan und Bluetooth und habe ihre Firmware geflasht nun starte ich ihre App leider wird der esp32 nicht im Bluetooth angezeigt muß ich irgendwas ändern

jens-software, 2020-07-18:
Kann man ihre Platine irgendwo erwerben

graham22, 2020-07-18:
You have to pair the esp32 with your phone before you launch the app
it should appear as HC-06 in the available bluetooth devices, if it asks
for a password, use 1234

On Sat, Jul 18, 2020 at 7:49 AM jens-software <notifications@github.com>
wrote:

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

--
Graham A. Ross
(613) 769-1331

graham22, 2020-07-18:
I have a few arduino nano version boards left that include the L298 motor
controller which is limited to 2 amps.
I didn't make a pcb for the ESP32 version since the ESP dev board has most
of what you need, you just have to connect it to the motor controller and
5v supply.

[image: image.png]

On Sat, Jul 18, 2020 at 8:22 AM jens-software <notifications@github.com>
wrote:

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

--
Graham A. Ross
(613) 769-1331

jens-software, 2020-07-18:
Können Sie mir Bilder davon schicken hätte Interesse an Ihrer Platine pn pfeiffermit@gmail.com

Closed 2020-07-28.

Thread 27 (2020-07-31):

Anzeige Sonnen Aufgang und untergang

jens-software, 2020-07-31:
Ist es möglich eine Anzeige für Sonnen Aufgang und Untergang in der App einzubauen

graham22, 2020-07-31:
You could probably calculate it but it might be easier to get the information from the internet using a service like  https://sunrise-sunset.org/api

Closed 2020-08-29.

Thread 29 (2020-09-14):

Can you describe the pinout? What are these pins used for?

Jestergnet, 2020-09-14:
Hello, please describe the pinout of these pins. What is connected for what and how...
Did I understand this limit switches correctly?

Anemometer Signal | GPIO34
-- | --
Motor Controller - Enable1 | GPIO12
Motor Controller - IN1 | GPIO13
Motor Controller - IN2 | GPIO14
Motor Controller - Enable2 | GPIO26
Motor Controller - IN3 | GPIO27
Motor Controller - IN4 | GPIO25

graham22, 2020-09-14:
Motor Controller - Enable1 GPIO12 - run the actuator when high
Motor Controller - IN1 GPIO13 - retract low, extend high
Motor Controller - IN2 GPIO14 - retract high. extend high

Enable1, IN1, IN2 -> horizontal actuator
Enable2, IN3, IN4 -> vertical actuator

IN1&2 set the direction if IN1 is low then IN2 is High
if you use a L298 then you need to wire both IN1 & IN2, if you use a
H-Bridge module like the one in the wiki
<https://github.com/ClassicDIY/SkyeTracker/wiki/3---ESP32>, then you only
need IN1 & Enable

[image: image.png]

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

--
Graham A. Ross
(613) 769-1331

Jestergnet, 2020-09-14:
It is very difficult to understand the translation from the translator.
Can I have a schematic diagram?
I use ESP32 and H Bridge.
Thank!

graham22, 2020-09-15:
There is a wiring diagram in the wiki
[https://github.com/ClassicDIY/SkyeTracker/wiki/3---ESP32](https://github.com/ClassicDIY/SkyeTracker/wiki/3---ESP32)

Closed 2020-09-17.

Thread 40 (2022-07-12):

Safety issue durin strong wind and initialization sequence

Robertarduino, 2022-07-12:
During sequence of initialization better to put panels in 90 dgr. In this case strong wind will not damage system. Park position sequence wait till initialization will not fish.

Closed 2023-09-23.

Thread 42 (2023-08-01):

Loosing settings

catalincre, 2023-08-01:
Hi, great work. I have a problem with my installation, if the esp32 is loosing power the settings are also lost. Thats an issue in a remote area with no constant power. Is there a way to make the settings permanent in the code like those for wifi?

graham22, 2023-08-02:
The settings are stored in non-volatile ram and should persist through a power cycle. The default setting will load on the following conditions;
1. if the factory reset pin is low (Pin 4)
2. if the checksum value is wrong indicating corrupt data.
3. The NVRam can't be loaded.

if you compile the code with "-D APP_LOG_LEVEL=ARDUHAL_LOG_LEVEL_DEBUG" in platform.ini, it will log to a serial monitor. This may help determine the issue.
The relevant code is in code/ESP32/src/Configuration.cpp -> void Configuration::Load()

catalincre, 2023-09-10:
Sorry, the settings are lost on two instance every time the esp is loosing power, after the new security update on samsung, can't open the app anymore on two phones, a s23 ultra and a flip 3.

graham22, 2023-09-18:
I have updated the google app to API 33 so it should work on most new phones.

catalincre, 2023-09-23:
It works now, thx. It can be closed.

Closed 2023-09-23.

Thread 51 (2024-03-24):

End Switch

Jeba0815, 2024-03-24:
it is possible to integrate limit switches. For example, I can't get all the way to the east.

graham22, 2024-03-25:
Your actuators need to have a built in limit switch, you should enter the Max East/West & Min/Max elevations using the android app so the code can more accurately calculate the step increments...

Closed 2024-03-25.

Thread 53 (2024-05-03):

Can't Build Firmware

Stein-N, 2024-05-03:
### Hey i tried changing AnemometerVoltageMin and Max Settings to another Value and build the Firmware but i get the Error that SPI.h is missing:

```console
Processing uno (board: nanoatmega328; platform: atmelavr; framework: arduino)
------------------------------------------------------------------------------------------------------------------------------------------------------------------------------------------------------------------
Removing unused dependencies...
Verbose mode can be enabled via `-v, --verbose` option
CONFIGURATION: https://docs.platformio.org/page/boards/atmelavr/nanoatmega328.html
PLATFORM: Atmel AVR (5.0.0) > Arduino Nano ATmega328
HARDWARE: ATMEGA328P 16MHz, 2KB RAM, 30KB Flash
DEBUG: Current (avr-stub) External (avr-stub, simavr)
PACKAGES:
 - framework-arduino-avr @ 5.2.0
 - toolchain-atmelavr @ 1.70300.191015 (7.3.0)
LDF: Library Dependency Finder -> https://bit.ly/configure-pio-ldf
LDF Modes: Finder ~ chain, Compatibility ~ soft
Found 10 compatible libraries
Scanning dependencies...
Dependency Graph
|-- ArduinoJson @ 7.0.4
|-- RTClib @ 2.1.4
|-- ArduinoThread @ 2.1.1
|-- Wire @ 1.0
|-- SoftwareSerial @ 1.0
Building in release mode
Compiling .pio\build\uno\src\Anemometer.cpp.o
Compiling .pio\build\uno\src\Configuration.cpp.o
Compiling .pio\build\uno\src\LinearActuatorNoPot.cpp.o
Compiling .pio\build\uno\src\Sun.cpp.o
Compiling .pio\build\uno\src\Tracker.cpp.o
Compiling .pio\build\uno\src\main.cpp.o
Compiling .pio\build\uno\liba7d\Wire\Wire.cpp.o
Compiling .pio\build\uno\liba7d\Wire\utility\twi.c.o
Compiling .pio\build\uno\lib460\Adafruit BusIO\Adafruit_BusIO_Register.cpp.o
Compiling .pio\build\uno\lib460\Adafruit BusIO\Adafruit_I2CDevice.cpp.o
Compiling .pio\build\uno\lib460\Adafruit BusIO\Adafruit_SPIDevice.cpp.o
Compiling .pio\build\uno\lib1f0\RTClib\RTC_DS1307.cpp.o
Compiling .pio\build\uno\lib1f0\RTClib\RTC_DS3231.cpp.o
Compiling .pio\build\uno\lib1f0\RTClib\RTC_Micros.cpp.o
Compiling .pio\build\uno\lib1f0\RTClib\RTC_Millis.cpp.o
Compiling .pio\build\uno\lib1f0\RTClib\RTC_PCF8523.cpp.o
In file included from .pio\libdeps\uno\Adafruit BusIO/Adafruit_BusIO_Register.h:10:0,
                 from .pio\libdeps\uno\Adafruit BusIO\Adafruit_BusIO_Register.cpp:1:
.pio\libdeps\uno\Adafruit BusIO/Adafruit_SPIDevice.h:9:10: fatal error: SPI.h: No such file or directory

*************************************************************
* Looking for SPI.h dependency? Check our library registry!
*
* CLI  > platformio lib search "header:SPI.h"
* Web  > https://registry.platformio.org/search?q=header:SPI.h
*
*************************************************************

 #include <SPI.h>
          ^~~~~~~
compilation terminated.
In file included from .pio\libdeps\uno\Adafruit BusIO\Adafruit_SPIDevice.cpp:1:0:
.pio\libdeps\uno\Adafruit BusIO\Adafruit_SPIDevice.h:9:10: fatal error: SPI.h: No such file or directory

*************************************************************
* Looking for SPI.h dependency? Check our library registry!
*
* CLI  > platformio lib search "header:SPI.h"
* Web  > https://registry.platformio.org/search?q=header:SPI.h
*
*************************************************************

 #include <SPI.h>
          ^~~~~~~
compilation terminated.
*** [.pio\build\uno\lib460\Adafruit BusIO\Adafruit_BusIO_Register.cpp.o] Error 1
*** [.pio\build\uno\lib460\Adafruit BusIO\Adafruit_SPIDevice.cpp.o] Error 1
src\Tracker.cpp: In member function 'void SkyeTracker::Tracker::ProcessCommand(const char*)':
src\Tracker.cpp:241:3: warning: 'template<unsigned int N> class ArduinoJson::V704L1::StaticJsonDocument' is deprecated [-Wdeprecated-declarations]
   StaticJsonDocument<256> root;
   ^~~~~~~~~~~~~~~~~~
In file included from .pio\libdeps\uno\ArduinoJson\src/ArduinoJson.hpp:53:0,
                 from .pio\libdeps\uno\ArduinoJson\src/ArduinoJson.h:9,
                 from include/Tracker.h:3,
                 from src\Tracker.cpp:1:
.pio\libdeps\uno\ArduinoJson\src/ArduinoJson/compatibility.hpp:63:58: note: declared here
 class ARDUINOJSON_DEPRECATED("use JsonDocument instead") StaticJsonDocument
                                                          ^~~~~~~~~~~~~~~~~~
=========================================================================================== [FAILED] Took 1.58 seconds ===========================================================================================
```

### But when i add SPI as a dependency in the platformio.ini i get the following error:

```console
Processing uno (board: nanoatmega328; platform: atmelavr; framework: arduino)
-----------------------------------------------------------------------------------------------------------------------------------------------------------------------------------------------------------------------------------
Verbose mode can be enabled via `-v, --verbose` option
CONFIGURATION: https://docs.platformio.org/page/boards/atmelavr/nanoatmega328.html
PLATFORM: Atmel AVR (5.0.0) > Arduino Nano ATmega328
HARDWARE: ATMEGA328P 16MHz, 2KB RAM, 30KB Flash
DEBUG: Current (avr-stub) External (avr-stub, simavr)
PACKAGES:
 - framework-arduino-avr @ 5.2.0
 - toolchain-atmelavr @ 1.70300.191015 (7.3.0)
LDF: Library Dependency Finder -> https://bit.ly/configure-pio-ldf
LDF Modes: Finder ~ chain, Compatibility ~ soft
Found 10 compatible libraries
Scanning dependencies...
Dependency Graph
|-- ArduinoJson @ 7.0.4
|-- RTClib @ 2.1.4
|-- ArduinoThread @ 2.1.1
|-- Wire @ 1.0
|-- SoftwareSerial @ 1.0
|-- SPI @ 1.0
Building in release mode
Checking size .pio\build\uno\firmware.elf
Advanced Memory Usage is available via "PlatformIO Home > Project Inspect"
RAM:   [=====Error: The program size (31316 bytes) is greater than maximum allowed (30720 bytes)
   *** [checkprogsize] Explicit exit, status 1
  ]  53.1% (used 1087 bytes from 2048 bytes)
Flash: [==========]  101.9% (used 31316 bytes from 30720 bytes)
```

### i was wondering if i miss something

Stein-N, 2024-05-03:
Oh nice thanks, was asked to change that but never used platformio.ini ever before or C++ in general

graham22, 2024-05-11:
Set versions for dependent libraries in platform.ini
added include for spi.h

Closed 2024-05-11.

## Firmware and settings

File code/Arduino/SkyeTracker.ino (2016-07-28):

#include <ArduinoJson.h>
#include <ThreadController.h>
#include <Thread.h>
#include <Wire.h> 
#include <SoftwareSerial.h>

#include "RTClib.h"
#include "sun.h"
#include "Configuration.h"
#include "Tracker.h"
#include "Trace.h"
#include "Anemometer.h"

using namespace SkyeTracker;

#define RECEIVE_BUFFER 200

RTC_DS1307 _rtc;
Configuration _config(&_rtc);
ThreadController _controller = ThreadController();
Tracker _tracker(&_config, &_rtc);
Anemometer _anemometer(A3);
Thread* _workerThread = new Thread();
SoftwareSerial _swSer(12, 13, false);

char* _receiveBuffer;
int _receiveIndex = 0;
int _protectCountdown = 0;
float _recordedWindSpeedAtLastEvent = 0;
uint32_t _lastWindEvent;

void setup()
{
	Serial.begin(9600); // HC-06 default baud rate
	while (!Serial) {
		; // wait for serial port to connect.
	}
	_swSer.begin(115200);
	//freeMem("At start of setup");
	trace(&_swSer, F("RAM At start of setup: "));
	traceln(&_swSer, String(freeRam(), DEC));
	Wire.begin();
	_rtc.begin();
	if (!_rtc.isrunning()) {
		traceln(&_swSer, F("RTC not running!"));
		_rtc.adjust(DateTime(2015, 6, 21, 12, 00, 0));
		_tracker._errorState = TrackerError_FailedToAccessRTC;
	}
	_lastWindEvent = 0;
	String d = "";
	DateTime now = _rtc.now();
	d = d + now.year() + "/" + now.month() + "/" + now.day() + " " + now.hour() + ":" + now.minute() + ":" + now.second() + "    ";
	traceln(&_swSer, d);
	traceln(&_swSer, F("Loading configuration"));
	_config.Load();
	// Configure main worker thread
	_workerThread->onRun(runWorker);
	_workerThread->setInterval(2000);
	_controller.add(_workerThread);
	traceln(&_swSer, F("Initializing tracker"));
	_tracker.Initialize(&_controller, &_swSer);
	_tracker.Track();
	_receiveBuffer = (char*)malloc(RECEIVE_BUFFER);
	//freeMem("At end of setup");
	traceln(&_swSer, F("RAM Completing setup: ") );
	traceln(&_swSer, String(freeRam(), DEC));
}

void loop()
{
	_controller.run();
	if (_tracker.getState() == TrackerState_Standby)
	{
		_tracker.Track();
	}
	serialEvent();
}

void runWorker()
{
	//freeMem("Run");
	//trace(&_swSer, F("RAM in Run: "));
	//traceln(&_swSer, String(freeRam(), DEC));
	bool broadcasting = _tracker.BroadcastPosition();
	if (_config.hasAnemometer())
	{
		float windSpeed = _anemometer.WindSpeed();
		if (_recordedWindSpeedAtLastEvent < windSpeed)
		{
			_lastWindEvent = _rtc.now().unixtime();
			_recordedWindSpeedAtLastEvent = windSpeed;
		}
		if (windSpeed > 8.0) // wind speed greater than 28.8 km/hour? (8 M/S *3600 S)
		{
			_lastWindEvent = _rtc.now().unixtime();
			_recordedWindSpeedAtLastEvent = windSpeed;
			_tracker.Park(true);
			_protectCountdown = 300; // 10 minute countdown to resume tracking
		}
		else if (--_protectCountdown <= 0)
		{
			_protectCountdown = 0;
			_tracker.Resume();
		}
		if (broadcasting)
		{
			Serial.print("Wind|{");
			Serial.print("\"sT\":"); // seconds in unixtime
			Serial.print(_lastWindEvent);
			Serial.print(",\"sC\":"); // current wind speed
			Serial.print(windSpeed);
			Serial.print(",\"sH\":"); // last high wind speed
			Serial.print(_recordedWindSpeedAtLastEvent);
			Serial.println("}");
		};
	}
}

void serialEvent() {
	
	while (Serial.available()) {
		char inChar = (char)Serial.read();
		_receiveBuffer[_receiveIndex++] = inChar;
		if (_receiveIndex >= RECEIVE_BUFFER)
		{
			Serial.print(F("receive buffer overflow!: "));
			_receiveIndex = 0;
		}
		else if (inChar == '\r') {
			//printHexString(_receiveBuffer);
			_receiveBuffer[_receiveIndex] = 0;
			_tracker.ProcessCommand(_receiveBuffer);
			_receiveIndex = 0;
		}
	}
}

// Debug helper functions
//
//void printHexString(String txt)
//{
//	for (int i = 0; i < txt.length(); i++)
//	{
//		trace(&_swSer, txt[i], HEX);
//	}
//	traceln(&_swSer, "");
//}


//Code to print out the free memory

//struct __freelist {
//	size_t sz;
//	struct __freelist *nx;
//};
//
//extern char * const __brkval;
//extern struct __freelist *__flp;
//
//uint16_t freeMem(uint16_t *biggest)
//{
//	char *brkval;
//	char *cp;
//	unsigned freeSpace;
//	struct __freelist *fp1, *fp2;
//
//	brkval = __brkval;
//	if (brkval == 0) {
//		brkval = __malloc_heap_start;
//	}
//	cp = __malloc_heap_end;
//	if (cp == 0) {
//		cp = ((char *)AVR_STACK_POINTER_REG) - __malloc_margin;
//	}
//	if (cp <= brkval) return 0;
//
//	freeSpace = cp - brkval;
//
//	for (*biggest = 0, fp1 = __flp, fp2 = 0;
//	fp1;
//		fp2 = fp1, fp1 = fp1->nx) {
//		if (fp1->sz > *biggest) *biggest = fp1->sz;
//		freeSpace += fp1->sz;
//	}
//
//	return freeSpace;
//}
//
//uint16_t biggest;
//
//void freeMem(char* message) {
//	trace(&_swSer, message);
//	trace(&_swSer, ":\t");
//	traceln(&_swSer, freeMem(&biggest));
//}

int freeRam()
{
	extern int __heap_start, *__brkval;
	int v;
	return (int)&v - (__brkval == 0 ? (int)&__heap_start : (int)__brkval);
}

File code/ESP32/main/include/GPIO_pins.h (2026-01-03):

#pragma once
#include <Arduino.h>

#ifdef EDGEBOX

void inline GPIO_Init() {}

// Programming and Debugging Port
#define U0_TXD GPIO_NUM_43
#define U0_RXD GPIO_NUM_44

// I2C
#define I2C_SDA GPIO_NUM_20
#define I2C_SCL GPIO_NUM_19

// I2C INT fro RTC PCF8563
#define I2C_INT GPIO_NUM_9

// SPI BUS for W5500 Ethernet Port Driver
#define ETH_SS GPIO_NUM_10
#define ETH_MOSI GPIO_NUM_12
#define ETH_MISO GPIO_NUM_11
#define ETH_SCK GPIO_NUM_13
#define ETH_INT GPIO_NUM_14
#define ETH_RST GPIO_NUM_15

// A7670G
#define LTE_AIRPLANE_MODE GPIO_NUM_16
#define LTE_PWR_EN GPIO_NUM_21
#define LTE_TXD GPIO_NUM_48
#define LTE_RXD GPIO_NUM_47

// RS485
#define RS485_TXD GPIO_NUM_17
#define RS485_RXD GPIO_NUM_18
#define RS485_RTS GPIO_NUM_8

// CAN BUS
#define CAN_TXD GPIO_NUM_1
#define CAN_RXD GPIO_NUM_2

// BUZZER
#define BUZZER GPIO_NUM_45

// Motor Controller
#define PWMa_H GPIO_NUM_13
#define ENABLE_H GPIO_NUM_12
#define PWMb_H GPIO_NUM_14
#define PWMa_V GPIO_NUM_27
#define ENABLE_V GPIO_NUM_26
#define PWMb_V GPIO_NUM_25

// Anemometer
#define AnemometerPin A0
#define ADC_Resolution 65536.0

#endif
#ifdef NORVI_GSM_AE02

#define BUTTONS GPIO_NUM_36 // Analog pin to read buttons

void inline GPIO_Init() { pinMode(GPIO_NUM_36, INPUT); }

// Programming and Debugging Port
#define U0_TXD GPIO_NUM_03
#define U0_RXD GPIO_NUM_01

// I2C
#define I2C_SDA GPIO_NUM_16
#define I2C_SCL GPIO_NUM_17

// GSM Modem
#define LTE_PWR_EN GPIO_NUM_21
#define LTE_TXD GPIO_NUM_32
#define LTE_RXD GPIO_NUM_33

// RS485
#define RS485_TXD GPIO_NUM_26
#define RS485_RXD GPIO_NUM_25
#define RS485_RTS GPIO_NUM_22

// OLED display definitions
#define SCREEN_ADDRESS 0x3C // OLED 128X64 I2C address
#define SCREEN_WIDTH 128    // OLED display width, in pixels
#define SCREEN_HEIGHT 64    // OLED display height, in pixels
#define OLED_RESET -1       // Reset pin # (or -1 if sharing Arduino reset pin)

// Motor Controller
#define PWMa_H GPIO_NUM_13
#define ENABLE_H GPIO_NUM_12
#define PWMb_H GPIO_NUM_14
#define PWMa_V GPIO_NUM_27
#define ENABLE_V GPIO_NUM_26
#define PWMb_V GPIO_NUM_25

// Anemometer
#define AnemometerPin A0
#define ADC_Resolution 4095.0

#endif

#ifdef Waveshare_Relay_6CH

#define RGB_LED_PIN 38
#define GPIO_PIN_Buzzer 21   // Buzzer Control GPIO
#define PWM_Channel 1        // PWM Channel
#define Frequency 1000       // PWM frequencyconst
#define Resolution 8
#define Dutyfactor 200

void inline RGB_Light(uint8_t red_val, uint8_t green_val, uint8_t blue_val) {
   neopixelWrite(RGB_LED_PIN, green_val, red_val, blue_val); // RGB color adjustment
}

void inline Buzzer_PWM(uint16_t Time) // ledChannel：PWM Channe    dutyfactor:dutyfactor
{
   ledcWrite(PWM_Channel, Dutyfactor);
   delay(Time);
   ledcWrite(PWM_Channel, 0);
}

void inline GPIO_Init() {
   pinMode(RGB_LED_PIN, OUTPUT);     // Initialize the control GPIO of RGB
   pinMode(GPIO_PIN_Buzzer, OUTPUT); // Initialize the control GPIO of Buzzer

   ledcSetup(PWM_Channel, Frequency, Resolution); // Set PWM channel
   ledcAttachPin(GPIO_PIN_Buzzer, PWM_Channel);   // Connect the channel to the corresponding pin
}
// UARTS
#define U0_TXD GPIO_NUM_43
#define U0_RXD GPIO_NUM_44

// RS485
#define RS485_TXD GPIO_NUM_17
#define RS485_RXD GPIO_NUM_18
#define RS485_RTS -1

// I2C
#define I2C_SDA GPIO_NUM_47
#define I2C_SCL GPIO_NUM_48

// Motor Controller
#define PWMa_H GPIO_NUM_1
#define ENABLE_H GPIO_NUM_12
#define PWMb_H GPIO_NUM_2
#define PWMa_V GPIO_NUM_41
#define ENABLE_V GPIO_NUM_11
#define PWMb_V GPIO_NUM_42

// Anemometer
#define AnemometerPin A0
#define ADC_Resolution 4095.0

#endif
#ifdef Lilygo_Relay_4CH

// I2C
#define I2C_SDA GPIO_NUM_15
#define I2C_SCL GPIO_NUM_14

// OLED display definitions
#define SCREEN_ADDRESS 0x3C // OLED 128X64 I2C address
#define SCREEN_WIDTH 128    // OLED display width, in pixels
#define SCREEN_HEIGHT 64    // OLED display height, in pixels
#define OLED_RESET -1       // Reset pin # (or -1 if sharing Arduino reset pin)

// Motor Controller
#define PWMa_H GPIO_NUM_21
#define ENABLE_H GPIO_NUM_22
#define PWMb_H GPIO_NUM_19
#define PWMa_V GPIO_NUM_18
#define ENABLE_V GPIO_NUM_23
#define PWMb_V GPIO_NUM_5

// Anemometer
#define AnemometerPin A0
#define ADC_Resolution 4095.0

#endif

#ifdef Lilygo_Relay_6CH

// HT74HC595
#define HT74HC595_CLOCK GPIO_NUM_5
#define HT74HC595_LATCH GPIO_NUM_6
#define HT74HC595_DATA GPIO_NUM_7
#define HT74HC595_OUT_EN GPIO_NUM_4

#define RTC_IRQ GPIO_NUM_18

// I2C
#define I2C_SDA GPIO_NUM_16
#define I2C_SCL GPIO_NUM_17

#ifdef Has_OLED
// OLED display definitions
#define SCREEN_ADDRESS 0x3C // OLED 128X64 I2C address
#define SCREEN_WIDTH 128    // OLED display width, in pixels
#define SCREEN_HEIGHT 64    // OLED display height, in pixels
#define OLED_RESET -1       // Reset pin # (or -1 if sharing Arduino reset pin)
#endif

// Anemometer
#define AnemometerPin A0
#define ADC_Resolution 4095.0

#endif

#ifdef ESP_32Dev

// I2C
#define I2C_SDA GPIO_NUM_21
#define I2C_SCL GPIO_NUM_22
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

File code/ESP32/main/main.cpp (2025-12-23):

#include "Arduino.h"
#include <esp_task_wdt.h>
#include <esp_system.h>
#include <ArduinoJson.h>
#include <WiFi.h>
#include <ThreadController.h>
#include <Thread.h>
#include <sys/time.h>
#include "time.h"
#include "Log.h"
#include "GPIO_pins.h"
#include "Defines.h"
#include "Configuration.h"
#include "Tracker.h"
#include "GPIO_pins.h"


using namespace CLASSICDIY;

ThreadController _controller = ThreadController();
Tracker _tracker = Tracker();

void setup() {
#ifdef ENABLE_H // disable actuators during initialization
   pinMode(ENABLE_H, OUTPUT);
   digitalWrite(ENABLE_H, false);
   pinMode(ENABLE_V, OUTPUT);
   digitalWrite(ENABLE_V, false);
#endif
   delay(3000);
   // wait for Serial to connect, give up after 5 seconds, USB may not be connected
   unsigned long start = millis();
   Serial.begin(115200);
   while (!Serial) {
      if (5000 < millis() - start) {
         break;
      }
   }

   logd("------------ESP32 specifications ---------------");
   logd("Chip Model: %s", ESP.getChipModel());
   logd("Chip Revision: %d", ESP.getChipRevision());
   logd("Number of CPU Cores: %d", ESP.getChipCores());
   logd("CPU Frequency: %d MHz", ESP.getCpuFreqMHz());
   logd("Flash Memory Size: %d MB", ESP.getFlashChipSize() / (1024 * 1024));
   logd("Flash Frequency: %d MHz", ESP.getFlashChipSpeed() / 1000000);
   logd("Heap Size: %d KB", ESP.getHeapSize() / 1024);
   logd("Free Heap: %d KB", ESP.getFreeHeap() / 1024);
   logd("------------ESP32 specifications ---------------");

   _tracker.Setup(&_controller);
   esp_task_wdt_init(60, true); // 60-second timeout, panic on timeout
   esp_task_wdt_add(NULL);
   logd("Free Heap after setup: %d KB", ESP.getFreeHeap() / 1024);
   logd("------------Setup Done ---------------");
}

void loop() {
   _tracker.Process();
   _controller.run();
   if (_tracker.getState() == TrackerState::Standby) {
      _tracker.Track();
   }
   esp_task_wdt_reset(); // Feed the watchdog
   delay(10);
}

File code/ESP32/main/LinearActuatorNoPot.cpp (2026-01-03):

#include "LinearActuatorNoPot.h"
#include "Log.h"

#ifdef Lilygo_Relay_6CH
LinearActuatorNoPot::LinearActuatorNoPot(String name, int relayOne, int relayTwo, std::shared_ptr<ShiftRegister74HC595<1>> reg) {
   _reg = reg;
   _name = name;
   _PWMa = relayOne;
   _PWMb = relayTwo;
   _requestedAngle = 0;
   _state = ActuatorState_Stopped;
   enabled = false;
   _currentPosition = 0;
   _lastTime = 0;
   _runTime = 0;
   _southernHemisphere = false;
}
#else
LinearActuatorNoPot::LinearActuatorNoPot(String name, int8_t enableActuator, int8_t PWMa, int8_t PWMb) {
   _name = name;
   _enableActuator = enableActuator;
   _PWMa = PWMa;
   _PWMb = PWMb;
   _requestedAngle = 0;
   _state = ActuatorState_Stopped;
   enabled = false;
   _currentPosition = 0;
   _lastTime = 0;
   _runTime = 0;
   _southernHemisphere = false;
}
#endif

LinearActuatorNoPot::~LinearActuatorNoPot() {}

float LinearActuatorNoPot::FlipAngle(float angle) { return _southernHemisphere ? 180 - ((angle > 180) ? angle - 360 : angle) : angle; }

void LinearActuatorNoPot::Initialize(int retractedAngle, int extendedAngle, int actuatorLength, int actuatorSpeed, bool southernHemisphere) {
#ifndef Lilygo_Relay_6CH
   pinMode(_enableActuator, OUTPUT);
   pinMode(_PWMa, OUTPUT);
   pinMode(_PWMb, OUTPUT);
#endif
   _southernHemisphere = southernHemisphere;
   _extendedAngle = FlipAngle(extendedAngle);
   _retractedAngle = FlipAngle(retractedAngle);
   _state = ActuatorState_Initializing;
   _actuatorLength = actuatorLength;
   _inchesPerSecond = actuatorSpeed / 100.0;
   Retract();
}

void LinearActuatorNoPot::run() {
   runned();

   if (_state == ActuatorState_Initializing) {
      _runTime = millis() - _lastTime;
      if (Travel() > _actuatorLength) {
         enabled = false;
         _currentPosition = 0;
         Stop();
         logi("%s actuator retracted and initialized", _name);
      }
   } else {
      float currentAngle = CurrentAngleFlipped();
      float delta = abs(currentAngle - _requestedAngle);
      // Serial.print(_name + F(" tracking currentAngle: "));
      // Serial.print(currentAngle);
      // Serial.print(F(" _requestedAngle: "));
      // Serial.print(_requestedAngle);
      // Serial.print(F(" delta: "));
      // Serial.print(delta);
      // Serial.print(F(" _currentPosition: "));
      // Serial.println(_currentPosition);
      if (delta <= histeresis) {
         Stop();
         logi("%s actuator tracking complete ", _name);
      } else if (currentAngle < _requestedAngle) {
         if (_state != ActuatorState_MovingOut) {
            MoveOut();
            _lastTime = millis();
            logi("%s actuator MoveOut ", _name);
         }
      } else if (currentAngle > _requestedAngle) {
         if (_state != ActuatorState_MovingIn) {
            MoveIn();
            _lastTime = millis();
            logi("%s actuator MoveIn ", _name);
         }
      }
      long now = millis();
      _runTime = now - _lastTime;
      _lastTime = now;
      if (_state == ActuatorState_MovingOut) {
         _currentPosition += Travel(); // inch step ((time in millis * 1000)  * speed
      } else if (_state == ActuatorState_MovingIn) {
         _currentPosition -= Travel(); // inch step ((time in millis * 1000)  * speed
      }
   }
}

float LinearActuatorNoPot::CurrentPosition() // inches from retracted position
{
   return _currentPosition;
}

float LinearActuatorNoPot::Travel() // inches travelled during runtime (now - _lastTime)
{
   float seconds = _runTime / 1000.0;
   return seconds * _inchesPerSecond;
}

float LinearActuatorNoPot::CurrentAngleFlipped() {
   if (_state == ActuatorState_Initializing) {
      return 0;
   }
   float delta = _extendedAngle - _retractedAngle;
   float degreesPerStep = delta / _actuatorLength;
   return (_currentPosition * degreesPerStep) + _retractedAngle;
}

float LinearActuatorNoPot::CurrentAngle() {
   return FlipAngle(CurrentAngleFlipped()); // facing north in southern hemisphere?
}

void LinearActuatorNoPot::Retract() {
   _requestedAngle = _retractedAngle;
   setInterval(longCheckInterval);
#ifdef Lilygo_Relay_6CH
   _reg->set(_PWMa, false);
   _reg->set(_PWMb, true);
#else
   digitalWrite(_PWMa, false);
   digitalWrite(_PWMb, true);
   digitalWrite(_enableActuator, true);
#endif
   _lastTime = millis();
   _state = ActuatorState_Initializing;
   enabled = true;
}

void LinearActuatorNoPot::MoveIn() {
#ifdef Lilygo_Relay_6CH
   _reg->set(_PWMa, false);
   _reg->set(_PWMb, true);
#else
   digitalWrite(_PWMa, false);
   digitalWrite(_PWMb, true);
   digitalWrite(_enableActuator, true);
#endif
   _state = ActuatorState_MovingIn;
}

void LinearActuatorNoPot::MoveOut() {
#ifdef Lilygo_Relay_6CH
   _reg->set(_PWMa, true);
   _reg->set(_PWMb, false);
#else
   digitalWrite(_PWMa, true);
   digitalWrite(_PWMb, false);
   digitalWrite(_enableActuator, true);
#endif
   _state = ActuatorState_MovingOut;
}

void LinearActuatorNoPot::Stop() {
#ifdef Lilygo_Relay_6CH
   _reg->set(_PWMa, false);
   _reg->set(_PWMb, false);
#else
   digitalWrite(_PWMa, false);
   digitalWrite(_PWMb, false);
   digitalWrite(_enableActuator, false);
#endif
   _state = ActuatorState_Stopped;
   enabled = false;
}

void LinearActuatorNoPot::MoveTo(float angle) {
   angle = FlipAngle(angle);
   if (abs(angle - CurrentAngleFlipped()) > POSITIONINTERVAL) {
      logi("Move %s  to: %.0f", _name, angle);
      if (angle > _extendedAngle) {
         angle = _extendedAngle;
      } else if (angle < _retractedAngle) {
         angle = _retractedAngle;
      }
      setInterval(shortCheckInterval);
      _requestedAngle = angle;
      enabled = true;
      char angle[16];
      sprintf(angle, "%.0f", _requestedAngle);
      char subtopic[32];
      sprintf(subtopic, "%sAngle", _name);
      // _iot.publish(subtopic, angle, false);
   }
}

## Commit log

2015-10-03 Initial commint
    [Configuration.h]
2015-10-06 Implemented support for android setup
    [Configuration.h]
2015-10-07 Added Android app, pcb and sketchup drawings
    [8L16.skp, Battery Box.skp, Configuration.h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]
2015-10-07 Update to includes
    Include "" to <>
    [Configuration.h]
2015-10-07 Added some pictures of pcb...
2015-10-13 Prep to support no pot actuator
    LinearActuator has the virtual methods that a concrete class should
    implement
2015-10-18 Completed tracker setup, moved strings to eeprom
    [Configuration.h]
2015-10-19 Fixed bug with sun calc, actuator, formatted readings
    [LinearActuatorNoPot.cpp, SkyeTracker.ino, Tracker.cpp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]
2015-10-19 Changed lookup for actuator lengths & speed
2015-10-26 Updated schematic to include 12V regulator
    [Part V6.2.csv]
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2015-12-12 Added DateTimeTab, fixed support for southern hemisphere
    [Configuration.h]
2015-12-12 Removed Actuator with Pot, not supported in new hardware
2015-12-12 Update pcb with SMD HC-06 chip
2015-12-25 Removed TimeZone, tracker now uses UTC time
    [Configuration.h]
2015-12-26 Added scroll view for small devices
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2015-12-28 Fixed actuator length bug
    [LinearActuatorNoPot.cpp]
2016-02-05 Updated schema
    [Part V7.csv, Parts Summary V7.csv, Parts Summary V7.xlsx]
2016-02-28 Added support for Anemometer
    [Configuration.h, Kid.csv]
2016-02-28 Update to wiki to include proto board
    [SkyeTracker.fzz]
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2016-06-12 Fixed crash in map tab
    [Part V8.csv]
2016-07-28 Fixed Limits page, added isDirty, updated netduino config
    [SkyeTracker.sdf]
2019-11-17 Initial checkin of ESP32 version
    [Configuration.h]
2020-01-27 Create hub.dxf
    Added hub plate cad
    [hub.dxf]
2020-03-08 Updated gerber for V8.0
    [#hub.dxf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]
2020-03-09 Moved factory defaults to #define
    [Configuration.h]
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2020-03-24 improve documentation for anemometer sensorVoltage calculation
2020-03-24 move bluetooth device name to build_flags
2020-03-31 Update pictures, cad
    [#hub.dxf, Bottom.dxf, hub.dxf]
2020-04-08 Port arduino code to VSCode - initial commit
    [Configuration.h]
2020-04-08 Reorganized arduino code
    [Configuration.h, SkyeTracker.sdf]
2020-04-08 Update to trace stm
    [Configuration.h]
2020-04-08 Updated fritzing
    [SkyeTracker.fzz]
2020-04-18 Reorganized folder structure
    [Configuration.h, SkyeTracker.sdf]
2020-04-18 Updated mechanical Autodesk drawings
    [HubPlate.ipt, PillowBlockBearing.ipt, Spindle.0004.ipt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]
2020-04-18 Moved constants to platform.ini
    [Configuration.h]
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2020-07-27 Simplified Location, DateTime upload
    [Configuration.h]
2020-07-28 Rolled back factoryDefault changes
    [Configuration.h]
2020-10-07 Updated parts list and pictures
    [8L16.skp, Battery Box.skp, Dual Axis Tracker Assembly.skp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]
2020-12-03 Updated version after bug fix
    [Anemometer.cpp]
2021-01-06 Fix IOTWebConf version to 2.3.1, updated version
    [SkyeTracker_ESP32.fzz]
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2025-11-26 Refactoring - Work in Progress
    [Configuration.h, default_16MB.csv, default_8MB.csv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]
2025-11-27 Add automatic geolocation via IP API
    Introduces a GeoLocate method in Configuration that uses a free IP geolocation API to set latitude and longitude automatically when the device is online. Updates Tracker to call GeoLocate on network 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
    [Configuration.h]
2025-11-27 Refactor settings handling and add relay 6CH support
    Replaces form submission with JSON-based settings endpoint, updates IOT and Tracker interfaces to use JsonDocument, and adds Lilygo Relay 6CH hardware definitions. Removes legacy board config, updates web UI with controller buttons, and improves style for new controls. Also refactors configuration to use double for latitude/longitude and updates platformio.ini with new relay 6CH environment.
    [Configuration.h]
2025-11-28 Refactor for Lilygo 6CH relay support and web config validation
    Added support for Lilygo_Relay_6CH hardware using ShiftRegister74HC595 in Device and LinearActuatorNoPot classes. Refactored actuator logic to use shift register for relay control. Updated Tracker to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
2025-11-28 Add real-time tracker state updates and control API
    Introduces a /control HTTP endpoint for tracker commands and a WebSocket-based mechanism to push tracker state updates to the frontend. Updates the UI to display tracker state and adds new control buttons. Refactors actuator initialization and state handling for improved feedback and error reporting. Adds error description helper and enhances CSS for new UI elements.
    [Tracker.cpp, Tracker.h]
2025-11-29 Refactor settings handling and add RTC support
    Reworked settings form submission and processing for network configuration, including unified JSON handling and improved web interface. Added RTC support for Lilygo_Relay_6CH, including time synchronization and factory reset via GPIO0. Removed obsolete form submission methods and streamlined state updates for WebSocket clients. Updated dependencies and configuration to support new features.
    [Configuration.h]
2025-11-29 Comment out DNS server logic and update UI handling
    DNS server-related code in IOT.cpp is commented out to disable captive portal DNS handling. Tracker.cpp now replaces the {script} placeholder for future app scripts. The network selector logic in IOT.htm is updated to use 'APMode' instead of 'apmode'. Also, .vscode is now ignored in .gitignore and the VSCode settings file is removed.
    [Tracker.cpp]
2025-12-01 Refactor logging and remove unused device configs
    Replaces custom JSON logging with serializeJsonPretty and removes the printFormattedJson helper. Increases WebLog buffer size for improved log handling. Cleans up Device.cpp by removing unused EDGEBOX and NORVI_GSM_AE02 code blocks. Deletes obsolete build environments from platformio.ini for edgebox-esp-100 and norvi-esp32dev, streamlining configuration.
    [Configuration.cpp, Device.cpp]
2025-12-02 Rename Has_OLED_Display to Has_OLED
    Updated all references of the preprocessor macro Has_OLED_Display to Has_OLED in Device.cpp, IOT.cpp, and platformio.ini for consistency and simplification.
2025-12-04 Refactor web assets and settings handling for ESP32
    Moved HTML, CSS, and JS assets from main/include to data directory and updated code to serve them from the new location. Replaced legacy settings endpoints and logic with separate /iot_fields and /app_fields endpoints for modular configuration. Updated board partition files to use default_4MB.csv. Refactored Modbus bridge settings and improved template processing for web UI. Removed obsolete CMakeLists.txt and IOT.htm files.
    [default_16MB.csv, default_4MB.csv, default_8MB.csv]
2025-12-05 Remove Modbus Bridge feature and related code
    Eliminated the Modbus Bridge configuration and all associated logic from the web UI, JavaScript, CSS, and C++ backend. Cleaned up IOT class, interface, and settings to remove bridge-specific fields a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
    [default_16MB.csv, default_4MB.csv, default_8MB.csv]
2025-12-08 Refactor OLED handling and update dependencies
    Moved OLED display logic to a dedicated Oled class and updated all related interfaces and usages. Removed direct Adafruit_SSD1306 usage from Device and IOT, now using Oled class methods via callback 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
    [noOTA_4MB.csv]
2025-12-09 Remove network status LED blink logic
    Deleted conditional code handling network status indication via WIFI_STATUS_PIN and RGB_LED_PIN. This simplifies the Run() method and removes hardware-dependent LED feedback for network state.
2025-12-13 Document Lilygo T-Relay-S3 wiring in README
    Added information for Lilygo T-Relay-S3 wiring.
2025-12-15 Revise SkyeTracker app and wiring sections in README
    Updated SkyeTracker documentation to reflect changes in app support and wiring information.
2025-12-16 Refactor tracker modes and states, enhance UI feedback
    Separated TrackerMode and TrackerState enums for clearer logic and improved state handling. Updated web UI and TFT display to show both mode and state, as well as sun and actuator details. Refactored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
2025-12-18 Refactor display interface and update usage
    Renamed IOledServiceInterface to IDisplayServiceInterface for broader display support. Updated all references and method names to use the new interface, and replaced getOledInterface with getDisplayInterface. Added countdown caching in IOT to reduce redundant display updates.
    [Tracker.h]
2025-12-19 Add wind speed display and refactor TFT/Tracker logic
    Wind speed is now displayed on the web UI and TFT screen if an anemometer is present. The Anemometer class now uses oversampled ADC reads and filtering for more stable output. TFT display logic is re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
2025-12-22 Added support for ESP32-S3
    [NoSPIFFS_4MB.csv]
2025-12-23 Refactor tracker state reporting and UI data fields
    Reworked the Tracker's JSON state publishing to provide separate fields for azimuth, elevation, horizontal/vertical extents and angles, and wind speed, replacing previous string-formatted values. Updated the web UI and TFT display logic to consume and present these new fields with improved formatting. Simplified MQTT state publishing to send the full JSON state. Removed unused lastMode/lastState tracking, and added actuator disable logic during initialization in main.cpp. Also enabled HasMQTT in platformio.ini for ESP32_S3 builds.
    [Device.cpp, Tracker.cpp, Tracker.h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]
2026-01-03 Migrate to IOT_LIB
    [Configuration.h]
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
